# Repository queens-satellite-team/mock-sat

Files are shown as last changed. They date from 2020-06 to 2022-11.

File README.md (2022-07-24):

# Mock CubeSat

The purpose of this repository is to house all software and hardware required to build a Mock-Sat. A Mock-Sat is the Queen's Space Engineering Team - Satellite's hardware and software development platform. A typical use case for this platform is that you have some program or code idea and want to see how it interacts within the spacecraft system, or have some hardware and need to see how it can be integrated within the spacecraft system, you can build a moc-sat and implement your idea on top of the basic design.

## Mock-Sat Functionality

The moc-sat has the following resources are available to users:

- 1-axis orientation control
- image capturing
- one way communication (send beacon signals)

Additional resources to be worked on include:
- system configuration files
- simple two way communication
- command and data handling
- power generation and control
- fault detections
- fault responses
- multi-axis orientation control

## Mock-Sat Repository Layout

### Data Folder
This folder contains all images and text data on board the Moc-Sat. It is broken down into data that is to be sent out via the communications system, and data that is being stored either for testing

### Docs Folder
This folder contains general information and documentation regarding the moc-sat. This includes datasheets and papers that provide some additional theory behind the moc-sat.

### Firmware Folder
This folder contains all software to be put on seperate Arduino and STM32 microcontrollers that implement the different systems available to the moc-sat such as the communications system and the attitude determination and control system.

### Hardware Folder
This folder contains all hardware files, pinout, and wiring diagrams required to build the moc-sat systems.

### Media Folder
This folder contains all images used within this repository.

### SRC (Source) Folder
This folder contains all code written for the moc-sat on the raspberry pi. This includes python implementations for all sub-sytems and the actuall mock-sat itself.

### Tasks Folder
This folder contains all the tasks that the satellite is to perform. See the README instructions in the folder for creating new and how to use them!

# Getting Started
Below are the following steps to setup the software and hardware of the mock-sat.

## Software Setup
### Prerequisites
1. You should have python version 3.7 or greater installed.
2. The raspberry pi should have the latest version of the [Raspberry Pi OS (Buster)](https://www.raspberrypi.com/software/) installed.

You can see what version of python you are using with the following command in a terminal:
```
python3 -V
```

And you can determine which instance of python (as you can have multiple) you are running with the following command in a terminal:
```
which python3
```

### Setting up the Repository
Perform the following steps within a terminal.

1. Clone the repository.
```
git clone https://github.com/queens-satellite-team/mock-sat.git
cd mock-sat/
```

2. Create a python virtual environment. 
```
python3 -m venv moc-sat-venv
```

3. Activate the virtual environment and install all of the required packages.

- a. If you are on MacOS or Raspberry Pi (Linux):
```
source moc-sat-venv/bin/activate
moc-sat-venv/bin/python3 -m pip install --upgrade pip
moc-sat-venv/bin/pip3 install -r requirements.txt
```

- b. If you are developing on Windows:
```
source moc-sat-venv/Scripts/activate
moc-sat-venv/Scripts/python3 -m pip install --upgrade pip
moc-sat-venv/Scripts/pip3 install -r requirements.txt
```

## Hardware Setup
The following hardware is required:
- BLDC Motor, power supply, and motor controller.
- Two transceivers, one for the mock-sat and one for the ground station.
- Raspberry Pi
- Raspberry Pi Camera
- An orientation sensor (MPU650)
- Three Arduinos
- A 1-Axis test bed for the satellite

Please see the README.md in the hardware directory within this repository for further instructions.

## Google Drive 

- https://drive.google.com/drive/folders/1PjCpiJ1GjcGLUgqpvl0FE0fzke4_DoX0?usp=sharing

Meeting notes, logistical documents and other files that may not be in this repository are kept on a
[Google Drive](https://drive.google.com/drive/folders/1PjCpiJ1GjcGLUgqpvl0FE0fzke4_DoX0?usp=sharinghttps://www.google.com). The drive has public view access. If you are a member of QSAT and would like full edit access, please request access on the drive or send an email to joshua.wade@queensu.ca. Or just message me on facebook or something. 

## Repository Style Guidelines
In order to have consistency in the repository we are following the [Google
style guidelines](https://github.com/google/styleguide). The repository is 
primarily [C++](https://google.github.io/styleguide/cppguide.html) and 
[Python](https://google.github.io/styleguide/pyguide.html) but another relevant
style guideline is the [filetypes and names](https://developers.google.com/style/filenames).
If languages other than this are introduced into the repository, please consult
the associated style guideline and adhere to it.

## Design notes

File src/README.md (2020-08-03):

### Source Directory
  - `cmake` CMake configuration files for Arduino-CMake
  - `firmware` Arduino code.
  - `img` Image to send and location to store received image.
  - `scripts` Python scripts.
  - `src` C++ code.

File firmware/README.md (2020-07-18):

# Firmware
This directory contains all source files related to Arduino development. The
build system that is being used is [Arduino CMake](https://github.com/queezythegreat/arduino-cmake).
If you would like to build the code, navigate to the /src directory.
```
mkdir build && cd build
cmake ..
make <name of executable>-upload
```
If you would like to monitor the serial port the executable was uploaded on, 
additionally run:
```
make <name of executable>-serial
```
To use the above command you must have [Picocom](https://linux.die.net/man/8/picocom)
installed. 

## Debugging
The `make <name of executable>-upload` command often fails with the dreaded:
```
avrdude: stk500v2_ReceiveMessage(): timeout
```
This means your system cannot communicate with the serial port that has been
specified, either it doesn't exist (i.e. nothing is plugged in) or another
device is blocking it. Make sure:
* You do not have the Arduino IDE open, this will block the serial port
* There are no other scripts or executables using the serial port
* The Arduino is plugged in
* You have permission to use this serial port on your system
If you are developing on Windows using WSLtty, the serial port can be finicky.
I would suggest following these [instructions](https://docs.microsoft.com/en-us/archive/blogs/wsl/serial-support-on-the-windows-subsystem-for-linux) and then uploading the "Hello World" serial writing example
using the Arduino IDE. Then you can confirm that the serial port is activated
and configured correctly. After that you should be able to build.

## Serial Monitoring
It can be useful to open a serial monitor. Since Arduino CMake requires Picocom,
it makes sense to use that. Modify the following command for your needs:
```
picocom -b 115200 -r -l /dev/ttyUSB0
```
To exit Picocom use <Ctrl-a><Ctrl-x>.
## Adding libraries
The build system will detect external libraries that you use if you install
them in `/usr/share/arduino/libraries`.

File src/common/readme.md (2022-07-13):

# Common 
This folder contains all the common files that can be shared acrosss all sub-system code.

# 1.0 Arduino
The Arduino base class provides serial and i2c communication methods to be shared across any system. 

- More information on serial communication between a raspberry pi and an Arduino can be found [here](https://roboticsbackend.com/raspberry-pi-arduino-serial-communication/)
- More information on i2c communication between a raspberry pi and an Arduino can be found [here]()

## 1.1 Usage
We are leveraging Python's [class inheritance](https://www.w3schools.com/python/python_inheritance.asp) so that all our systems (radio, reaction wheel, etc.) can have the same communication method between the raspberry pi and the Arduino microcontrollers that implement the system. We can create a Python class that represents a system and inherent all methods from the Arduino class as seen below:

```
class Radio(Arduino):
    '''Radio sub-system to control an RF24 radio.
    '''

    def __init__(self):
        super().__init__()  # call the init function of the parent Arduino class
    
    def transmit(self, data:str):
        self.send_over_serial(data) # use the Arduino's class method to send over serial
```

## 1.2 Hardware Connections
Use the following image to setup the hardware connection between the raspberry pi and the Arduino.Be careful during this step! Arduinos use 5V-logic and Raspberry Pis use 3V3-logic. Fortunatly, the Raspberry Pi has internal pull-up resistors on the I2C lines, which pull the bus up to 3.3-volts. As long as you don’t connect any devices that pull the levels up to 5-volts you will be OK. You should also note that Arduino has open-collector outputs. Because of this, the Arduino logic levels on its I2C bus will be set to the levels of the pull-ups, which in this arrangement are in the Raspberry Pi. However, this does not work for serial communication! Please note the logic level converter in the Serial GPIO photo.

### 1.2.1 Serial (USB)

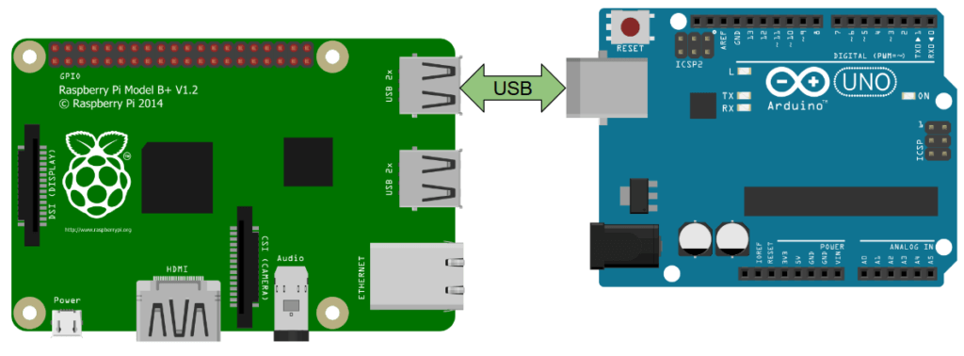
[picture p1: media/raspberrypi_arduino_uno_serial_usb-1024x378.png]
serial_pi_arduino


### 1.2.2 Serial (GPIOs)
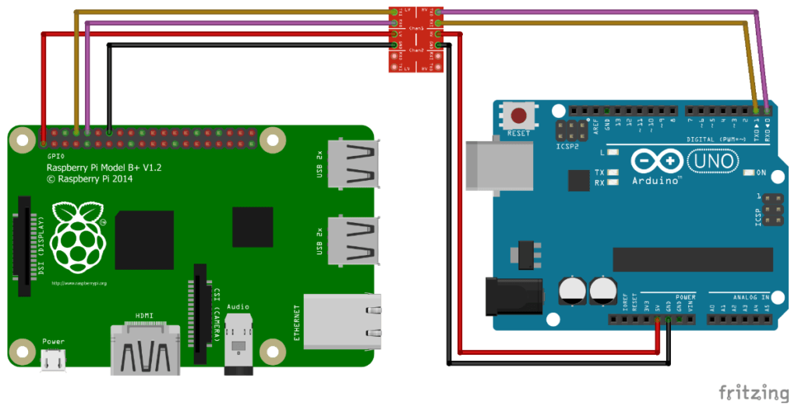
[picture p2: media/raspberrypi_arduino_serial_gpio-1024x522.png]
serial_pi_arduino


### 1.2.3 I2C (GPIOs)
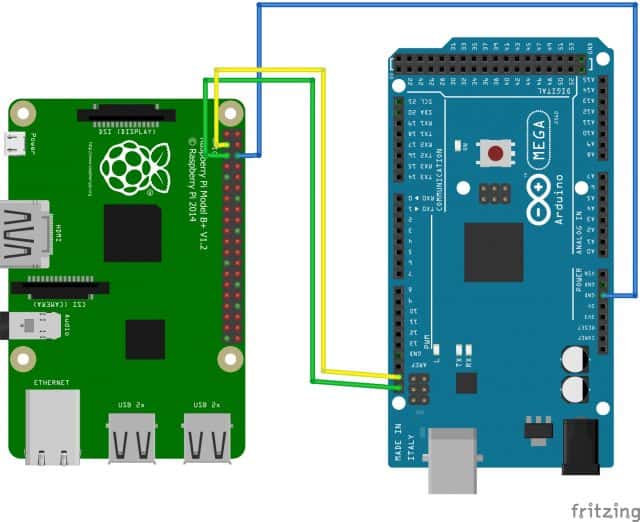
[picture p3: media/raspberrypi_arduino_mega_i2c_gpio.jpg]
serial_pi_arduino


# 2.0 Satellite
This is our mock-sat python object. It reflects all the hardware capabilities of the mock-sat, and provides the functionality to control these hardware features. The mock-sat object is available to all tasks scheduled by the OBC task manager and can thus use all methods and attributes of the class. 

# 3.0 Logger
This is our main way to log and print out all debug, info, warning, and critical messages. This class prints messages to the terminal screen (stdout), and saves it to a log file called by defualt "logger.log".

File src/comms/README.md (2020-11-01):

# Mock Sat - Communications

The purpose of this repository is to keep track of work and issues while building the communication software for a working (non-flight ready) satellite.

## Implementation

Four files are required to operate the MOC-SAT Communications. These include:

1. ground_station.py
2. ground_station.ino

3. satellite.py
4. satellite.ino

### ground_station.py

Opens a GUI that enables the user to send various commands to the connected tranceiver. The GUI has a serial monitor that can read data received from the connected arduino through the serial connection.

Upload this script to a computer (base station) and change hardware settings under CONFIGURATION in file.

### ground_station.ino

The connected Arduino and radio receives command from GUI and implements the respected command. The Arduino first sends an OP_CODE to the satellite's transeiver and then waits to receive data from the satellite.

Upload this script to the arduino (base station) and change hardware settings under Hardware Config and Radio Config in file.

### satellite.py

Reads an OP_CODE from the connected transceiver and executs an instruction according to it.

Upload this script to a rasperryPi (satellite) and change hardware settings under CONFIGURATION in file.

### satellite.ino

The connected Arduino and radio receives command from the base station transeiver and forwards it to the OBC (satellite.py). The Arduino then transmits the data corresponding to the received OP_CODE to the ground station transeiver.

Upload this script to the arduino (satellite) and change hardware settings under Hardware Config and Radio Config in file.

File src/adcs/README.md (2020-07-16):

The following scripts rely on:

-the RPi.GPIO library for python control of raspi IO pins (often comes pre-installed on raspi)
-the adafruit_bno055 library (for reading BNO055 sensor)
-all other libraries should be installed with python3

`BNO055_TEST.py` 
-tests the i2c connection between the raspi and the BNO055 sensor (currently tested with DFRobot's Gravity BNO055 sensor)

`FIT0441_TEST.py`
-tests the PWM control of the FIT0441 motor + controller unit - note that PWM uses pin 18 as that is the only harware PWM pin on the raspi 3B+

`MAX_TRQ.py`
-generates maximum change in reaction wheel momentum - used to test viability of testing platform

`PID_TEST.py`	***DISCONTINUED***
-initial attempt at PROPORTIONAL control of satellite orientation (single axis) - discontinued due to faulty testing bed (1st iteration gimbal)

`P_TEST.py`	***DISCONTINUED***
-second attemp at PROPORTIONAL control of satellite orientation (single axis), attempted patches for faulty testing bed - discontinued due to dampening of testing bed (2nd iteration gimbal)

`PI_TEST.py`
-partially working PROPORTIONAL-INTERGRAL control of satellite orientation (single axis) - tested using string testing bed

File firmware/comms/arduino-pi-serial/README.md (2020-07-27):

# Arduino-Pi comms testing

I'm currently working on reading files from the raspberry pi and sending to an arduino nano via serial port.

Serial comms between the pi and nanos is working, but needs to be made more robust.
The current nRF24 comms is happening with a simple transmit/receive data spam setup.
I've been testing using nRF24 ACK packets which seem to do the trick for bidirectional communication, just have to get it working properly and put all the pieces together.

It's taking a little longer than expected and the code is unorganized right now. I'll try to right a better setup guide and organize everything once it's all working

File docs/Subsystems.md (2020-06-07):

# QSET - Satellite Team Subsystems

A CubeSat can be broken into six major subsystems: structure, communication, power, attitude determination and control, command and data handling, and the payload. In the past, QSAT has had an exec team of managers for each subsystem and a CTO. QSAT&#39;s goal is to create a CubeSat that can rotate itself and take pictures at given orientation. This involves designing and building each of the subsystems and the computer system that would connect them.

[More info on CubeSat Subsystems](https://www.fictiv.com/blog/posts/satellite-101-what-is-a-cubesat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,data%20handling%2C%20and%20the%20payload.)

## ADCS – Attitude determination and Control System

&quot;_The attitude determination and control system (ADCS) controls the orientation of the CubeSat with respect to an inertial frame of reference and includes reaction wheels, magnetorquers, thrusters, star trackers, sun and Earth sensors, angular rate sensors and GPS receivers and antennas. This complex system is needed because when the satellite is first deployed, for example via NanoRacks from the International Space Station, it is tumbling. Some CubeSats can operate in this state, but others require pointing accuracy and location knowledge.&quot;_

During the first CSDC that Queen&#39;s participated in, the CubeSat only required passive attitude stabilization. (For this reason, the ADCS was just a couple long magnets.) The new ADCS requires active attitude actuation and momentum dumping. The current design includes a setup with 10 sun sensors, a BNO055 Absolute Orientation Sensor, 4 reaction wheels (1 redundant) and 3 magnetorquers. The goal is for the ADCS to provide precise attitude control with the reaction wheels and detumbling with the magnetorquers.

## _Comms – Ground to Sat Communications System_

&quot;_The communications system (COM) is severely limited by the amount of power available, which is usually around 2W. Compared to Boeing&#39;s 702SP Spacecraft, which uses a Xenon Electrostatic ion thruster system (XIPS), operates in the low- to mid-power range of satellites, and has three to eight kilowatts of power, CubeSats&#39; power is exponentially less._

_CubeSats use radio-communication systems in VHF, UHF, F-, S-, C- and X-band. The satellite uses an antenna, usually deployed once in orbit to help with communication. Antennas range from commercial measuring tape to more complicated inflatable dish antennas.&quot;_

## _EPS – Electrical Power System_

&quot;The electrical power system (EPS) consists of solar panels and batteries. Solar panels hold solar cells that convert the solar light from the sun to electricity. Batteries take up a lot of mass and volume on the already tightly packed CubeSat. A major design challenge is placing the solar panels, either on the sides of the CubeSat itself, or having deploying solar panels. Having deployable panels adds solar cell area but also an extra mechanical complexity. For the panels to deploy, they need a burn wire release mechanism, and every mechanical system adds the possibility of a failure. If the panel does not deploy properly, the CubeSat will not have any power and even if everything else is functioning properly, the CubeSat will fail due to the lack of power.&quot;

## _OBC – Onboard Computer System_

The OBC is the system that runs the CubeSat&#39;s software and connects and controls all the other subsystems. &quot;An OBC primarily consists of a microprocessor, memory banks and interfacing chip to connect the computer to other sub-systems.&quot;

Last year, most of the work and research on the OBC involved designing a system that was radiation hardened with redundant processors and bit voting logic. This was intended to rectify potential bit switching caused by ionizing radiation in LEO. Unfortunately, the complexity this created is beyond the scope of what QSAT is trying to accomplish this year, so the focus will be on creating a traditional OBC.

[More OBC info](https://blog.satsearch.co/2020-03-11-overview-of-on-board-computers-available-on-the-global-space-marketplace)

## _Payload – Camera and Telescope_

&quot;_The payload, or the purpose of the CubeSat, dramatically varies, depending on the type of mission required. These can include cameras for pictures or video, like Planet Labs, or space qualification of certain electronic components, testing of a flight control system, or even some type of biological experiment.&quot;_

QSAT&#39;s current mission is to create a satellite that can take pictures of the Earth. For this reason, the payload is essentially a camera sensor and a focusing lens. Pictures taken by the camera also need to be stored on the sat until they can be downlinked to the command station.

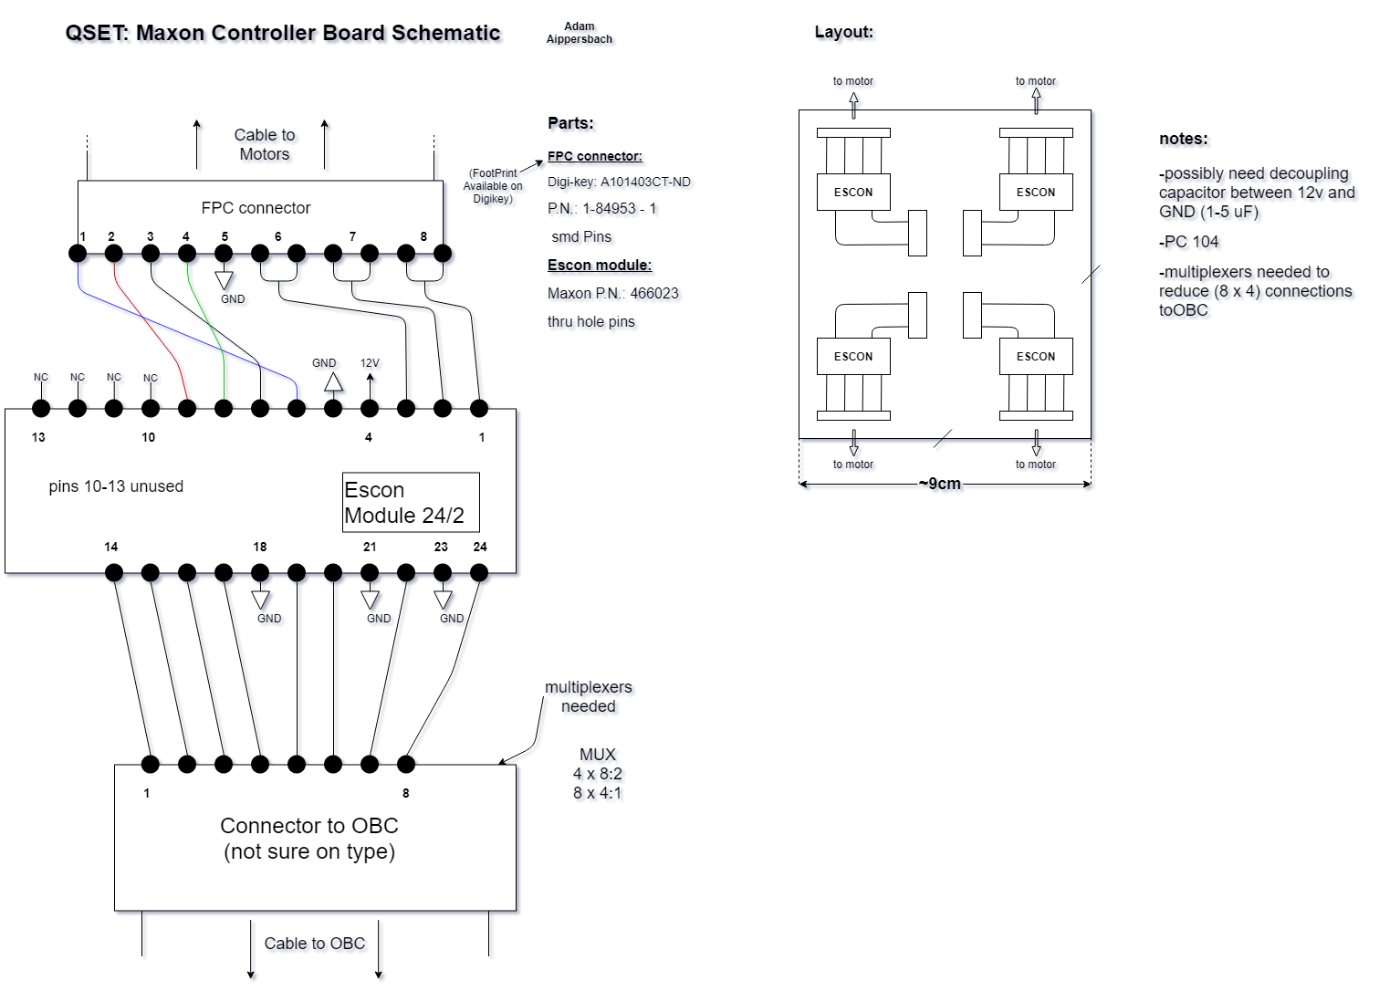
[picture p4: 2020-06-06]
docs/ADCS/Schematics/Maxon Controller Board Schematic.png

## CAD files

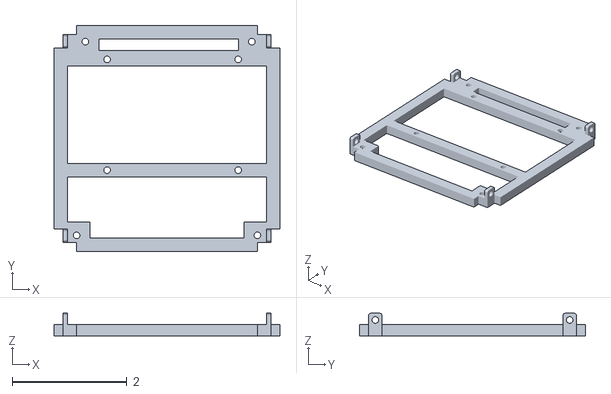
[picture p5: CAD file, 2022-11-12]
hardware/mock-sat-1U/stl/shelf-rpi.stl
3.94 x 3.94 x 0.394

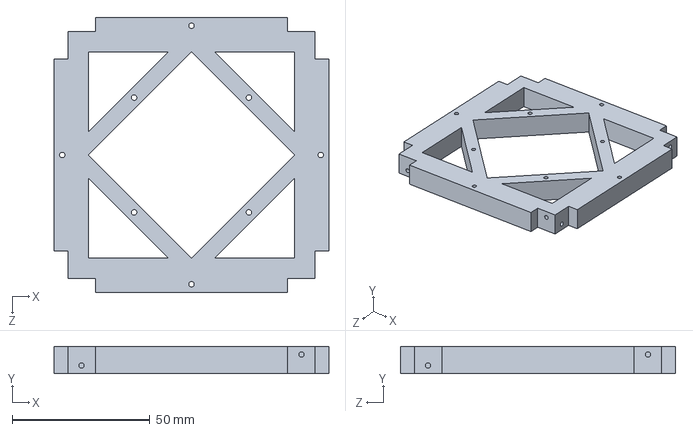
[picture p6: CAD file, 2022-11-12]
hardware/mock-sat-chassis/baseplate 2.SLDPRT
100.0 x 10.0 x 100.0 mm

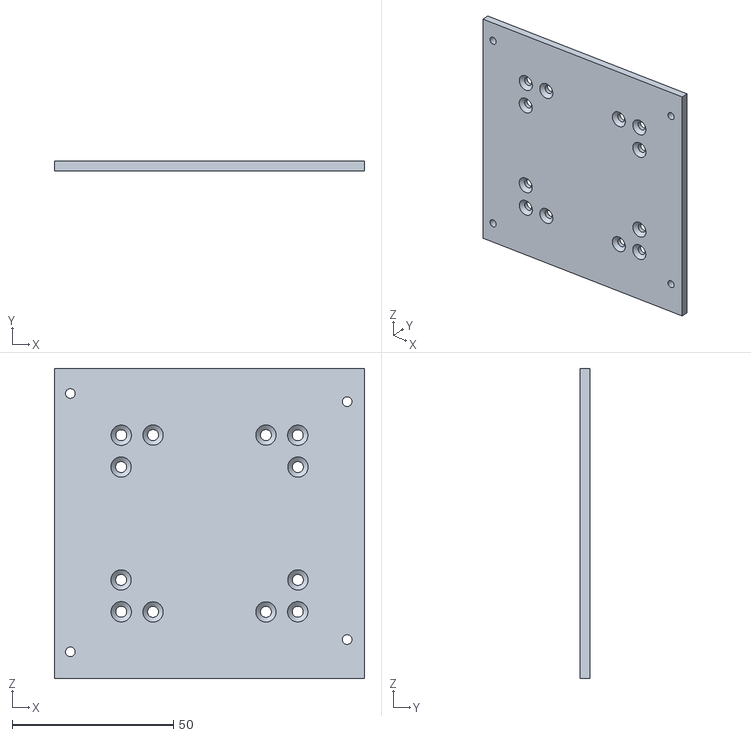
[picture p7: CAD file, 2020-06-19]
hardware/satellite-frame/base-plate-pc104.stl
96.0 x 3.00 x 96.0

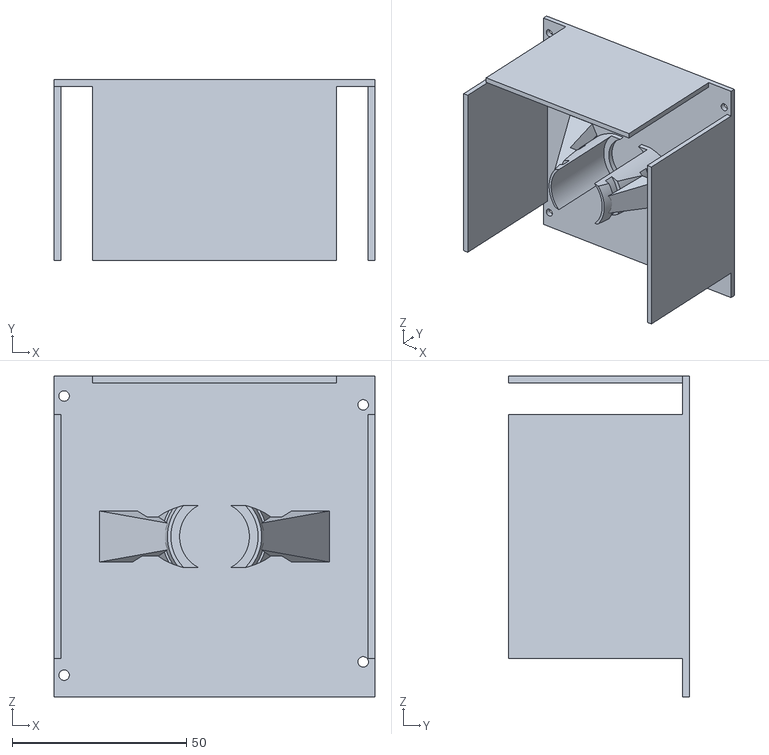
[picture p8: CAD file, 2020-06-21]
hardware/testing-gimbal/prototype/fit0411-motor-frame.stl
92.0 x 52.0 x 92.0

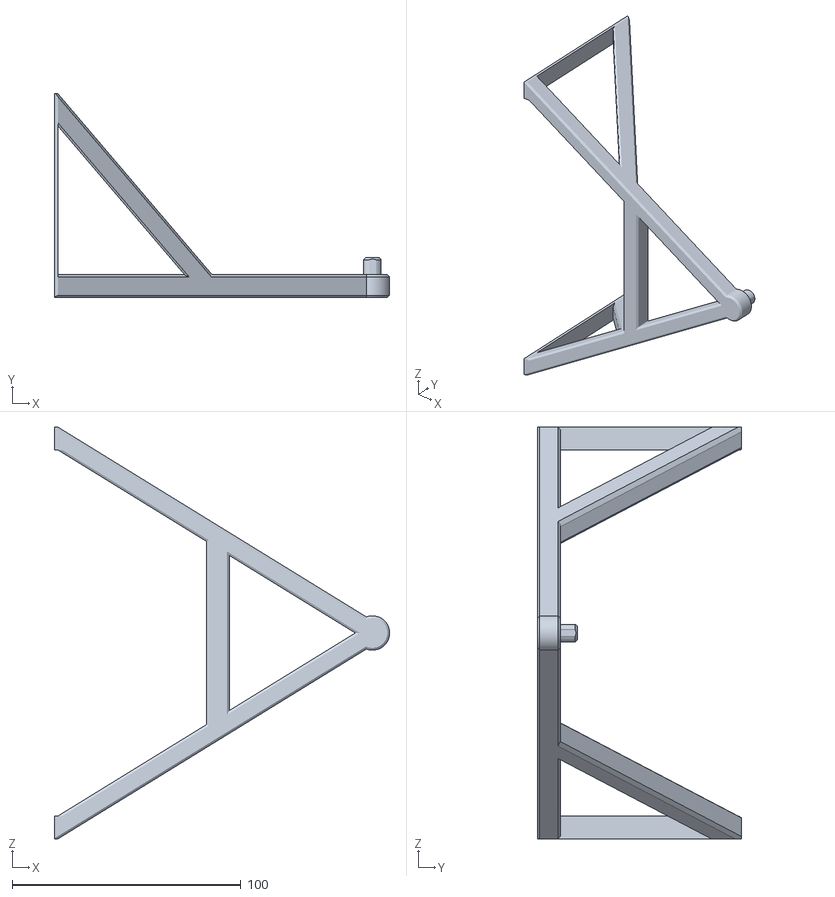
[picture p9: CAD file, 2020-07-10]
hardware/testing-gimbal/secondary-model/GimbalMk2 - gimbal base-1.STL
146.5 x 89.2 x 180.0

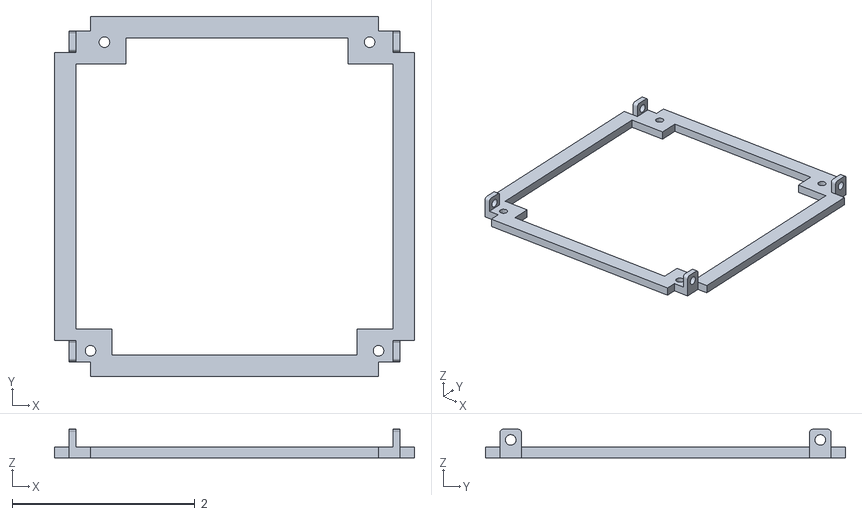
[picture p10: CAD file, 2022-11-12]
hardware/mock-sat-1U/stl/shelf-blank.stl
3.94 x 3.94 x 0.315

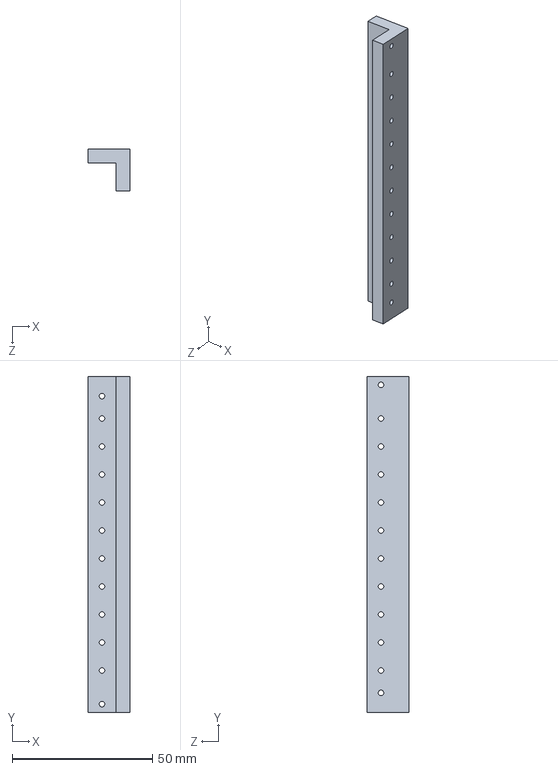
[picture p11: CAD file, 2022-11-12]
hardware/mock-sat-chassis/Siderib-U.SLDPRT
15.0 x 120.0 x 15.0 mm

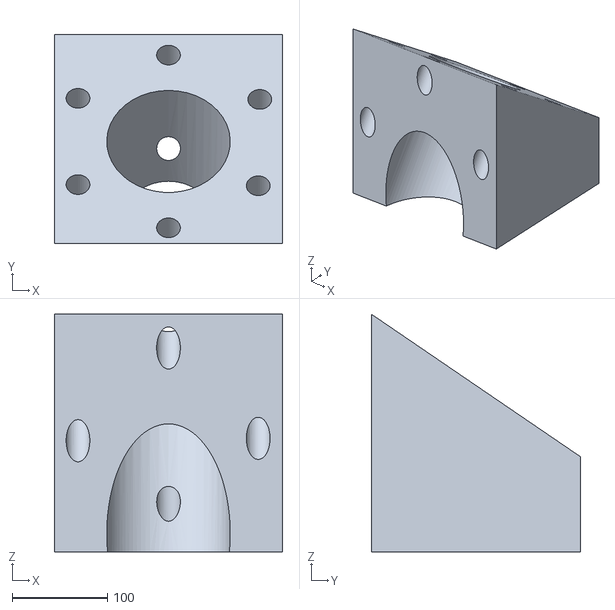
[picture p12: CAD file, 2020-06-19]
hardware/satellite-frame/reaction-wheel-mount.stl
240.0 x 220.0 x 250.0

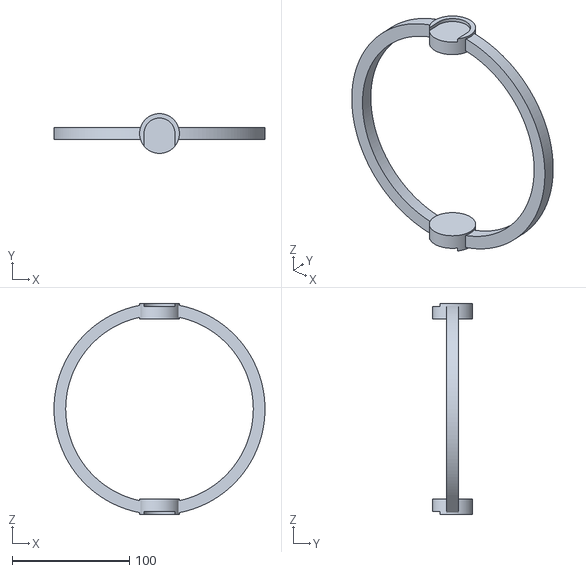
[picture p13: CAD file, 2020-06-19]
hardware/testing-gimbal/prototype/inner-ring-1.stl
180.0 x 34.0 x 180.0

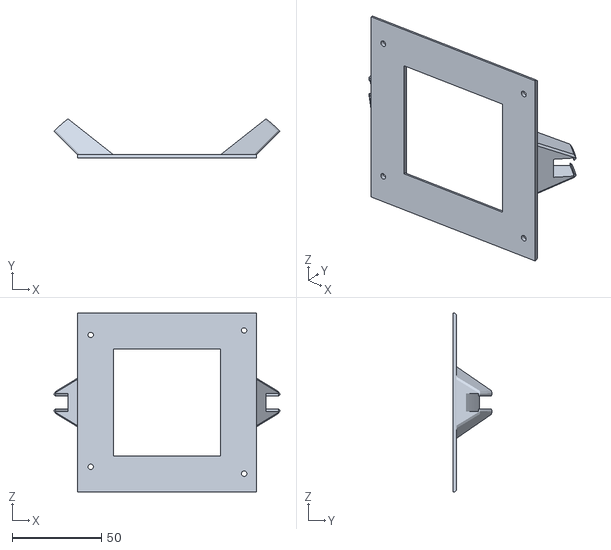
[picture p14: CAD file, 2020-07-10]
hardware/testing-gimbal/secondary-model/GimbalMk2 - connection-1.STL
126.3 x 22.0 x 100.0

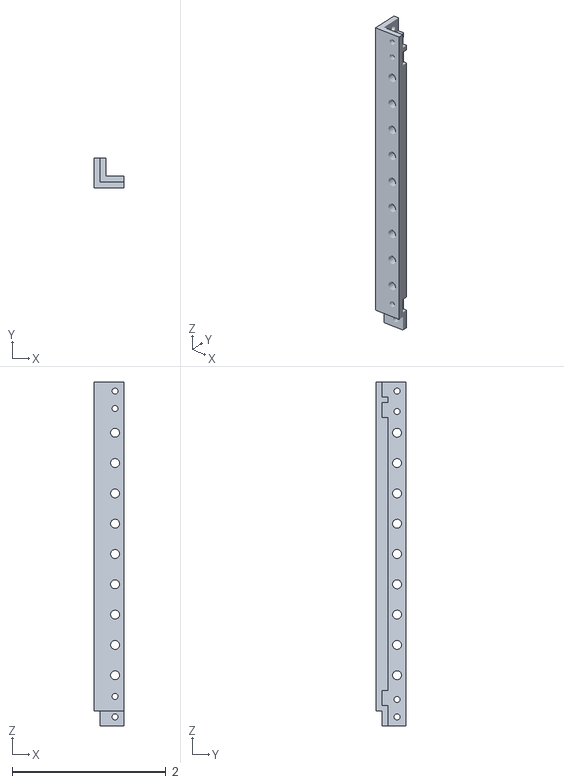
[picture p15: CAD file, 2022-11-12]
hardware/mock-sat-1U/stl/rail.stl
0.394 x 0.394 x 4.47

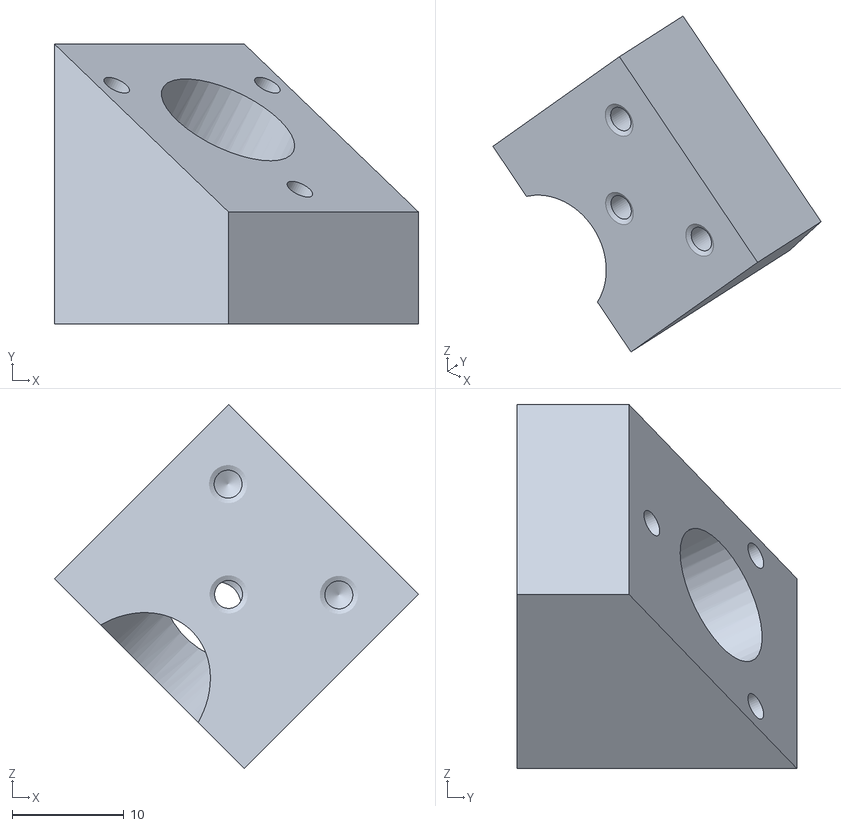
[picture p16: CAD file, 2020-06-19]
hardware/satellite-frame/motor-base.stl
32.5 x 25.0 x 32.5

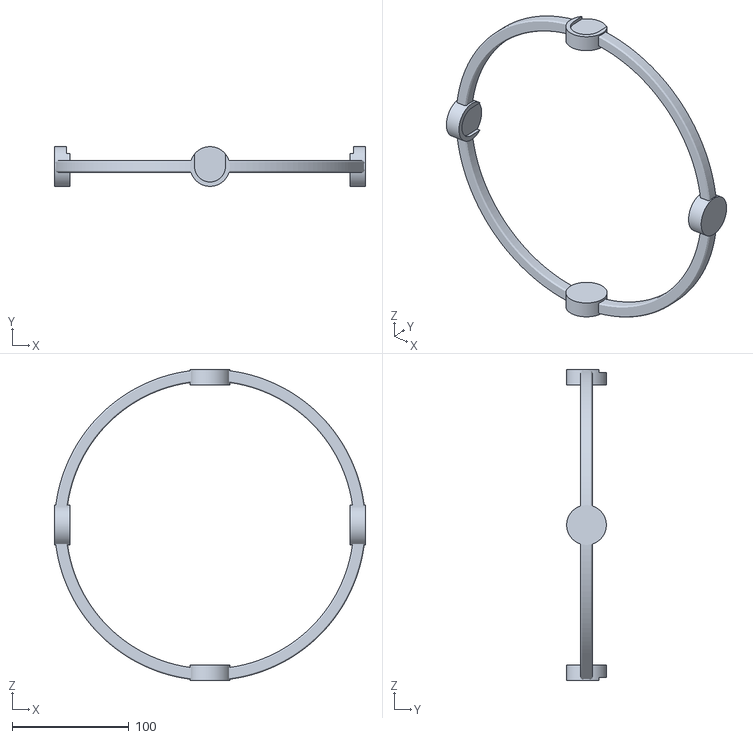
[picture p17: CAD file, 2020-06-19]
hardware/testing-gimbal/prototype/outer-ring-1.stl
266.0 x 34.0 x 266.0

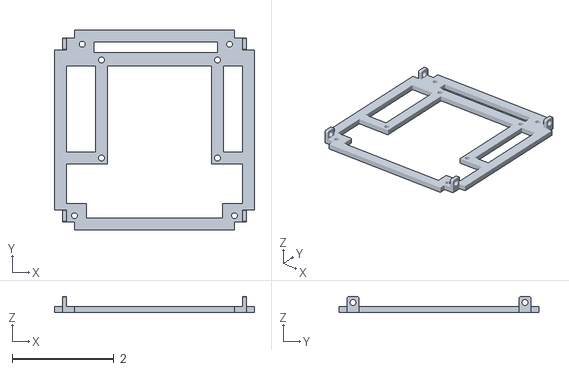
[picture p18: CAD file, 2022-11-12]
hardware/mock-sat-1U/stl/shelf-rpi-2.stl
3.94 x 3.94 x 0.315

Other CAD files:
hardware/testing-gimbal/secondary-model/GimbalMk2 - connection2-1.STL
hardware/satellite-frame/reach-wheel-base-plate.stl
hardware/testing-gimbal/prototype/outer-bearing-clip-1.stl
hardware/testing-gimbal/secondary-model/GimbalMk2 - outer section mk2-1.STL
hardware/mock-sat-1U/stl/rack.stl
hardware/mock-sat-1U/stl/shelf-nucleo.stl
hardware/mock-sat-1U/stl/shelf-protoboard.stl
hardware/mock-sat-chassis/Siderib-U.STL
hardware/testing-gimbal/prototype/inner-bearing-clip-1.stl
hardware/testing-gimbal/prototype/mid-ring-1.stl
hardware/testing-gimbal/secondary-model/GimbalMk2 - KFL08-1 608RS-1.STL
hardware/testing-gimbal/secondary-model/GimbalMk2 - inner section mk2-1.STL
hardware/testing-gimbal/secondary-model/GimbalMk2 - mid section mk2-1.STL

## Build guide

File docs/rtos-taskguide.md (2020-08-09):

List of tasks to run on Arduino FreeRTOS for moc-sat single axis system
-

1. ADCS read and control

    - read BNO055 (through I2C)
    - read Light Sensors
    - read Current Motor Data (read two analog)
    - set enable and direction (set two digital)
    - set desired vel (PWM for arduino or analog through I2C DAC)
    - set desired acc (analog through I2C DAC)

2. Focus and take photo

    - currently a raspi cam, will this work via arduino?
      - if not should we have a master raspi to take photos when the arduino returns okay?
      - would we be able to setup communication with the pi while using FreeRTOS?

3. Transmission of desired direction vector

    - is the transmitter controlled by SPI? 
    - this value should be given to ADCS function (then perhaps increase ADCS function priority?)

4. Transmission of photo information

    - likely the most intensive function/operation
    - can this be set as a 'background process' do be done in chunks? or should it be done all at once?
    
5. Emergency stop

    - simply a high priority function that can read a button or remote signal and stop all processes

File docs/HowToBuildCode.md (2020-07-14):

### Arduino Code
The Arduino code uses the [Arduino CMake](https://github.com/queezythegreat/arduino-cmake)
build system. To make sure the build system is working correctly perform the
following:
#### Linux
* Install CMake and the Arduino SDK. Install `picocom` if you do not already
  have it by running `sudo apt install picocom`. `picocom` is the default
  serial monitor for the build system.
* Connect an Arduino Mega 2560 to your computer. If you are going to connect
  a different Arduino, you must edit the `BOARD` parameter in
  `test/CMakeLists.txt` to reflect the Arduino you are using. If the Arduino
  is using a port other than `/dev/ttyACM0` you must change the `PORT` parameter
  in the same file.
* In the root of the repository, run the following commands:
  ```
  mkdir build && cd build    # create a build directory
  cmake ..                   # run CMake on the parent CMakeLists.txt
  make upload                # upload the firmware to the Arduino
  make hello_world-serial    # run a Picocom terminal to monitor the serial port
  ```
  You should see `Hello World!` being printed every second. To exit the picocom
  terminal, press Ctrl-a Ctrl-x.
#### WSLtty
WSLtty does offer support for communicating with hardware through serial ports.
WSL automatically maps the `COM<N>` ports on Windows to `/dev/ttyS<N>` ports. 
For example, `COM7` would be mapped to `/dev/ttyS7`. You can check which `COM`
port is being used by going into `Device Manager` and checking the 
`Ports (COM & LPT)` header in Windows. If the port being used is `COM7`, then
you must run:
```
sudo chmod 666 /dev/ttyS7
```
then follow the instructions for Linux. Check [this](https://docs.microsoft.com/en-us/archive/blogs/wsl/serial-support-on-the-windows-subsystem-for-linux) for more information.

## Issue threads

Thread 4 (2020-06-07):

Get hardware and tools from QSET room

JoshW7, 2020-06-07:
Email Simon to request temporary access to QSET room. We probably wont be able to get access again, so I need a full list of everything we need for the summer. I can include this list in the email to Simon.

**For Moc-Sat:**
- BLDC Motor, power supply, and motor controller
- Raspberry Pi
- Raspberry Pi Camera
- An orientation sensor
- An Arduino (I also have one of these at home if I can't find any in the room for some reason)

**Also Need:**
- Pelican case with Satellite and other expensive components
- Wires
- Wire cutters
- breadboards
- simple electrical components like resistors, caps
- Maybe soldering equipment

JoshW7, 2020-06-19:
Got most of what was listed, except for Raspberry Pi and capacitors. Pictures of every borrowed item on the [Google Drive](https://drive.google.com/drive/folders/1FAAZQhhic6-W0kydOLPNARDHKofG3PDZ?usp=sharing).

Closed 2020-06-19.

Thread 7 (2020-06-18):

Send low resolution image between transceivers

anthonysteel, 2020-06-18:
Send a low resolution image downloaded from the internet between the transceivers.

anthonysteel, 2020-06-18:
I am going to try a black and white image first.

anthonysteel, 2020-06-18:
It looks like I need to save the image on an SD card, load the image from the SD card onto the Nano and then send the image in packets through the transceiver. I bought [these](https://www.amazon.ca/Gikfun-Storage-Memory-Arduino-EK1442C/dp/B071D5BFKD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).

anthonysteel, 2020-06-21:
I am now using a Mega connected to the SD card and a Nano connected to the nRF24L01 transceiver.  The reason for having two Arduino's is that both the SD card and transceiver communicate using SPI and there is only one SPI port on the Mega/Nano. I am going to try and connect the two boards via I2C.

anthonysteel, 2020-06-25:
I am going to close this issue. To resolve this issue there are actually several sub-issues which are better organized in a project.

Closed 2020-06-25.

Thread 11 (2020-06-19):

Write P Controller to Rotate Satellite in Gimbal

anthonysteel, 2020-06-19:
Convert controller previously used in simulation to controller on satellite.

WoJiaoCal99, 2020-07-16:
Semi-functional PI control working with FIT0441 motor and low-torque (string) testing bed 73f6b52cfca69930f2f6613d548babe2d8815373 .

Closed 2020-07-16.

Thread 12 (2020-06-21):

Find way to work with Soldiworks part files collaboratively

anthonysteel, 2020-06-21:
Part and assembly files are usually large. If you put them in a Github repository it will make pulling and pushing extremely slow especially because git diff won't work on part files. We should decide on a work around for this.

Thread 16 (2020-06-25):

Send Image from SD Card to transceiver on MocSat

anthonysteel, 2020-06-25:
The MocSat has two arduinos, a Mega and a Nano. The Nano is connected to the transceiver and the Mega is connected to an SD card storing the image. The two MocSat Arduinos communicate through an I2C connection. Send the image from the SD card on the Mega to the Nano.

anthonysteel, 2020-07-15:
I stopped using the SD card because it introduced another Arduino unnecessarily. The SD card connection was happening over SPI and there is only one SPI port on the Arduino, which is currently being used by the transceiver. Right now the image is sent over serial to the Arduino. In future an SD card can be incorporated.

Closed 2020-07-14.

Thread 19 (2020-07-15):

Change send/receive scripts to accept ports as inputs

anthonysteel, 2020-07-15:
Right now the ports that the Arduinos are connected on are hard coded in the CMakeLists and in `send.py` / `receive.py`. Change these to accept the port as an input for easier development across machines.

anthonysteel, 2020-07-15:
For example, in the CMakeLists.txt file there is the following:
```
generate_arduino_firmware(server
    SKETCH server.cpp
    PORT /dev/ttyS9
    SERIAL picocom @SERIAL_PORT@
    BOARD mega2560)

generate_arduino_firmware(client
    SKETCH client.cpp
    PORT /dev/ttyS9
    SERIAL picocom @SERIAL_PORT@
    BOARD mega2560
```
which generates two executables, client and server. It would be better if port was specified at build time. Something like:
```
cmake --send-port /dev/ttyS8 --receive-port /dev/ttyS9 ..
```
CMake should have support for this kind of thing, or it can be set as an environment variable which CMake captures.

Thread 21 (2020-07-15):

Add message protocol to transceivers

anthonysteel, 2020-07-15:
As mentioned in #17, some of the image is being lost in transmission. This means it is time to implement some sort of data link layer. [Radiohead](https://www.airspayce.com/mikem/arduino/RadioHead/) seems promising and has support for our nRF24L01. I am going to start by trying to get this [client](https://www.airspayce.com/mikem/arduino/RadioHead/nrf24_client_8pde-example.html) and [server](https://www.airspayce.com/mikem/arduino/RadioHead/nrf24_server_8pde-example.html) example working.

anthonysteel, 2020-07-15:
Got example uploaded to Arduinos in 443d3faa84f1599c5d784021dcd5d4ff76f27415. Example is not working, the transceivers don't seem to able to find each other right now.

anthonysteel, 2020-07-15:
Problem solved, tutorial working, see 2d72ee69961a20e90f34b8c51f3ce3120cf100dc.

anthonysteel, 2020-07-15:
I know have a better understanding of how the transceiver code should work. The Arduino's should blindly read information from the serial port when it is available and blindly read information from the transceivers when it is available. This means that the code for both transceivers can be the same. I pushed this change in 3734c5e0c75544b7baac2652d4e5c5ac71579424.

anthonysteel, 2020-07-16:
Check out how to get [KISS](https://pypi.org/project/kiss/) for python working later. I tried the example but the library seems to be failing right now. The scripts throws a:
```
AttributeError: 'Frame' object has no attribute 'text'
```
from the APRS python package.

Closed 2020-07-18.

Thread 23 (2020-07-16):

Create new STL files for mounting maxon motor and drivers to sat frame

WoJiaoCal99, 2020-07-16:
Design a mount for prototyping with a single maxon motor and driver instead of FIT0441 motor

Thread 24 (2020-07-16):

Get single axis PI control loop working with maxon motor

WoJiaoCal99, 2020-07-16:

WoJiaoCal99, 2020-07-19:
Good [article ](https://www.maxongroup.co.uk/maxon/view/news/How-to-configure-a-maxon-ESCON-Speed-Controller) for basics of configuring maxon controller

WoJiaoCal99, 2020-07-19:
Motor [Datasheet ](http://edge.rit.edu/edge/P13021/public/DDR/Maxon%20Generator%2030W.pdf)

WoJiaoCal99, 2020-07-19:
[Page](https://www.maxongroup.com/maxon/view/content/escon-detailsite) for download of maxon controller setup software

anthonysteel, 2020-07-20:
Looks good.

WoJiaoCal99, 2020-07-23:
The [controller](https://www.maxongroup.com/maxon/view/product/control/4-Q-Servokontroller/466023) requires multiple inputs as specific signals:
-desired angular velocity (analog or digital PWM)
-angular acceleration (analog)
-direction (digital)
-enable (digital)
-all outputs come as analog
The raspi can only create digital and PWM signals (PWM with limited accuracy), thus cannot set angular acceleration. Simplest solution is probably an i2c slave to read and write analog signals and relay back to raspi.

WoJiaoCal99, 2020-07-23:
The motor connects via flex-cable (FPC cable) and needs an adapter for prototyping. [This 11-pin adapter](https://www.digikey.ca/en/products/detail/1-1734248-1/A101417CT-ND/2567553?itemSeq=333183093) should have the right spacing for the 5 normal width connections, and 3 wide (motor winding) connections on the flex cable.

WoJiaoCal99, 2020-08-06:
A few developments for maxon motor control:
-Previous adapter is a surface mount connector for PCBs. [This version](https://www.digikey.ca/en/products/detail/te-connectivity-amp-connectors/1-84982-1/1893492) should have enough space for soldering and prototyping.
-[This DAC](https://www.digikey.ca/en/products/detail/maxim-integrated/MAX11300PMB1%23/4914312?productid=4914312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) currently only works with the [Munich GUI Software](https://www.maximintegrated.com/en/design/software-description.html/swpart=SFW0004100C) on a laptop. [This library](https://os.mbed.com/teams/MaximIntegrated/code/MAX113XX_Pixi/shortlog/) seemed promising but hasn't worked with the raspi thus far. It should be noted that the DAC can be used as an oscilloscope and analog/digital signal IO and would be useful to have working with either raspi/arduino for both prototyping and potentially sensor/motor control in the final version of the moc-sat.
-Moving forwards with the [Sparkfun MCP4725 DAC](https://www.sparkfun.com/products/12918). If we can create our own i2c communication protocol with the chip, we could print our own on a custom PCB based on the [public design](https://github.com/sparkfun/MCP4725_Breakout/tree/v14).
-Moving from raspi to arduino for compatibility with the new DAC, as well as future development including RTOS and integration with the OBC subteam.

WoJiaoCal99, 2020-08-14:
Motor is now working:
-acc and vel are controlled by two MCP4725 DACs
-second flex-cable connection can be soldered for motor connections
-All i2c connections have been tested with arduino's [freeRTOS](https://www.freertos.org/a00110.html) and work - see commit 09b34a6a7239b34cd3f976704b3c3b82ddb7321e
-Moving forwards by creating control loop function to be run by the RTOS

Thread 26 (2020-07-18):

Create a packet format and checksum for transceivers

anthonysteel, 2020-07-18:
I was able to get an image sent between the two Arduinos using a physical I2C connection. The program for this was very simple. Parse the stream of bytes coming from the image file into buffers that do not exceed the serial buffer on the Arduino. Then have code on the Arduinos to receive bytes over I2C and send them onto the serial port.

However, when I tried to use the same program over the transceivers, a bunch of bytes were dropped. There could be more than one reason for this, but I think that implementing some kind of message protocol between the Arduino's would be the easiest solution.

The current code for the Arduino's is [here](https://github.com/queens-satellite-team/moc_sat/blob/master/src/firmware/transceiver.cpp) and looks like this:
```C++
#include <Arduino.h>
#include <SPI.h>
#include <RadioHead.h>
#include <RadioHead/RHGenericSPI.h>
#include <RadioHead/RH_NRF24.h>

RH_NRF24 nrf24(8, 53);
uint8_t data[RH_NRF24_MAX_MESSAGE_LEN];
uint8_t read_byte = 1;

void setup() {
  Serial.begin(9600);
  while (!Serial);
  if (!nrf24.init()) Serial.println("init failed");
  if (!nrf24.setChannel(1)) Serial.println("setChannel failed");
  if (!nrf24.setRF(RH_NRF24::DataRate2Mbps, RH_NRF24::TransmitPower0dBm))
    Serial.println("setRF failed!");
}

void loop() {
  int i = 0;
  while (Serial.available()) {
    if (i < RH_NRF24_MAX_MESSAGE_LEN) {
      data[i] = Serial.read();
      i++;
    } else {
      nrf24.send(data, sizeof(uint8_t)*i);
      nrf24.waitPacketSent();
      i = 0;
    }
  }
  if (i != 0) {
    nrf24.send(data, sizeof(data));
    nrf24.waitPacketSent();
  }
  while (nrf24.available()) {
    nrf24.recv(data, &read_byte);
    Serial.print(char(data[0]));
  }
}
```
Basically, if bytes are in the serial buffer, send them on the transceiver. If there are bytes in the transceiver buffer send them on serial. The same code can be run on both Arduino's and flashed once. I think this has a lot of upsides for development, and if we can get the image sending using the same Arduino code on the transceivers, that would be really great.

The scripts that parse the files into buffers and sends them over serial is [here](https://github.com/queens-satellite-team/moc_sat/tree/master/src/scripts/comms). The scripts are conveniently called `send.py` and `receive.py`.

In order to handle the seemingly lossy Bluetooth connection, I think we have to define a packet structure. We should implement the [KISS](https://en.wikipedia.org/wiki/KISS_(TNC)) protocol. Basically, choose a character to be a frame begin and end character `0xC0` . Choose a simply algorithm to make a check sum, for example, split each byte into a nibble, XOR all the bytes in the data buffer. Send the message as:
```
 0xC0 - checksum byte - some predefined number of data bytes - 0xC0.
```
Then have a byte that is dedicated as an acknowledge command. One of the scripts sends the message, the other checks the check sum and sends an ack command, if the ack is not sent in a predefined timeout, the message is resent. This should be relatively simple to implement.  The special command bytes, like frame header and acknowledge, will have to be escaped inside the data bytes. The protocol talks about this. Without this if 0xC0 was to appear in the data, there is no way to know if that was meant to be a frame end or actually 0xC0.

@JoshW7, can you tackle this problem?

anthonysteel, 2020-07-22:
See https://github.com/queens-satellite-team/moc_sat/issues/28#issuecomment-662189579

Closed 2020-07-22.

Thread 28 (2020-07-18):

Send image from Raspberry Pi SD card with NRF24L01 Transceiver

JoshW7, 2020-07-18:
I got an Arduino nano with a NRF24L01 set up to work from the Raspberry pi. The nano couldn't communicate with the R Pi using the default linux IDE so I installed the ARM version of Arduino 1.8.0 following this [forum thread](https://www.raspberrypi.org/forums/viewtopic.php?t=170210).

I installed the same nRF24 library on the pi and successfully sent serial data to my laptop using the transceivers.

Once we get [lossless data transmission](https://github.com/queens-satellite-team/moc_sat/issues/26) working, it should be easy to set up on the pi.

anthonysteel, 2020-07-20:
Another option for people working on this if they have a problem with flashing their Arduino using the Raspberry Pi: you can flash the Arduino using any computer or IDE that supports it and then just connect it to the RP, using the RP only for non-firmware development. Assuming that the Arduino code is relatively stable and won't need to be updated frequently,  this is a reasonable option.

I agree once, we get the lossless data transmission working it should carry over with no problems.

JoshW7, 2020-07-22:
RF24 has a built in acknowledgement (ACK) feature that allows for data packets to be sent without data loss. If you have the Arduino RF24 library installed, you can look at some of the ACK example sketches.

This is essentially a built in system for bi-directional communications and I believe it's what we're looking for. I'm going to mess around with sending huge data streams this way and see how fast/lossless it is. If all goes well, I'll try it with an image.

anthonysteel, 2020-07-22:
Perfect.

anthonysteel, 2020-07-22:
I’m going to close out #26 and we can re-open it if the built in R24 functionality fails.

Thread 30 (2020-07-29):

Order parts for EPS

anthonysteel, 2020-07-29:
Decide on what tutorial we are going to follow, and what parts are required. Write a BOM and push it to MocSat docs.

anthonysteel, 2020-07-29:
@varnikaagupta Was [this](https://www.digikey.ca/en/maker/projects/charge-batteries-with-an-arduino/b9d6ff74ecea437da8126d097d680d56) the tutorial Josh was talking about? You will also want to order a soldering iron, solder, rosin flux, solder remover and/or solder wick.

varnikaagupta, 2020-07-30:
Yep, I'll go through and get down all the equipment needed

varnikaagupta, 2020-07-30:
> Decide on what tutorial we are going to follow, and what parts are required. Write a BOM and push it to MocSat docs.

@anthonysteel Since we want to incorporate solar charging for the moc sat, would it be better to start directly with a tutorial like this? https://create.arduino.cc/projecthub/igorF2/solar-charged-battery-powered-arduino-uno-645d89
What voltage solar cells do we currently have?

anthonysteel, 2020-08-11:
Sorry for the late response to this. I don't know which solar cells are in the room, @JoshW7 might know, but I wouldn't worry about using the proper panels. That tutorial looks good, and yes I would say it is preferable to use panels directly.

You will also want to look at what methods there are for a controlled discharge of the batteries when you are testing the circuit. It might be something as simple as connecting them to a motor or light.

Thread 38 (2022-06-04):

Support Arduino Interface Class

SeanTedesco, 2022-06-04:
# Motivation
The Mock-Sat sub-systems are controlled by Arduino microcontrollers. We should have an easy python interface that supports basic communication with Arduinos for all the supported communication protocols.

# TO DO 📖
- [x] Create common directory
- [x] create Arduino base class
- [x] create serial tx and rx functions
- [x] create i2c tx and rx functions
- [x] implement class in comms RF24 parent class
- [x] include readme that demonstrates how-to-use and required setup.

SeanTedesco, 2022-07-13:
The class has been made and implemented. While the instructions can be added to they're good enough to get started.

Closed 2022-07-13.

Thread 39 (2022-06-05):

Mock-Sat Instructions

SeanTedesco, 2022-06-05:
# Motivation ⛰️
If the Mock-Sat is to be used as a development tool, team members must know how to use the tool. This issue will track the necessary work to create instructional content for the Mock-Sats.

# Implementation Ideas 💡
 - I am under the impression that the best way to learn to use a tool is to use it.
 - Stay away from making it a lab, and more of a technology demonstration. This is not meant to be a second Space School.
 - Every folder should have a README page.
- If we are to make more than one of these, we should have a mock-sat "bring up" page (how to build one).

# Steps Forward 🚶‍♂️
- [ ] Create a list of the required functionality for the Mock-Sat.
- [ ] Create initial demonstration / explanation for each functionality.
- [ ] Have a member give feedback and try to use the mock-sat with the previous demonstration/explanation.
- [ ] Iterate demonstration / explanation.
- [ ] Create videos for demonstration / explanation purposes.

# Completion Criteria 💯
- _Have a second/third year make a mock-sat and begin experimenting_

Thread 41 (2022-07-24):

Template Issue

SeanTedesco, 2022-07-24:
### Template Issue To-Do List
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

# Motivation ⛰️
> Provide a short description of the issue and explain why it is required to work on this issue.

# Next Steps 🚶
> Provide a list of steps for someone to complete in order to finish the issue.

- [ ] this is step one
- [ ] this is step two
- [ ] this is step three

# Supporting Material and Resources 📖
> If any links, resources, or past work would be useful include the links here

- [Markdown Style Guide for Creating Issues](https://www.markdownguide.org/basic-syntax/)

# Definition of Done 💯
> Be specific. There should be a concrete change that occurs after this issue is closed. Something is simplified, created, modified, replaced, enhanced, etc.

### Tags
> tag people that should know about this issue

cc: @SeanTedesco @emmapaczkowski

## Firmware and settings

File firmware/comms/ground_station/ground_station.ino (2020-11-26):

/***********************************************************************************/
/******************************** INCLUDES AND GLOBALS *****************************/
#include <SPI.h>
#include <RF24.h>

byte addresses[][6] = {"1Node", "2Node"};

/* globals for loop() */
bool newCommand = false;
String command;

/* globals for recvFromGS() */
bool newData = false;
const byte numChars = 32;
char receivedChars[numChars];

/* global data structure - maximum of 32 bytes can be sent as a packet */
struct dataStruct
{
  /* TYPE        NAME                  USE           BYTE LOCATION    */
  char flag;             //(command / data)           [0]
  char op_code;          //(command number)           [1]
  uint8_t data_len;      //(length of data)           [2]
  uint8_t data_start;    //(character to start)       [3]
  char data[20];         //(actual data)           [4:23]
  unsigned long _micros; //(return trip time)     [24:27]
  uint8_t data_end;      //(character to end)        [28]
} dataPack;

/***********************************************************************************/
/********************************** USER CONFIG ***********************************/
// Radio configuration
// 0 or 1 to distinguish between GRS = 0 and SAT = 1
bool radioNumber = 0;  // sets writing and reading pipe addresses
bool role = 1;         // 1 = transmit, 0 = receive
uint8_t channel = 100; // frequency channel

// Hardware configuration
RF24 radio(8, 10); //CE, CSN
/***********************************************************************************/
/*************************************** setup() ***********************************/
void setup()
{
  configSerial();
  configDataPack();

  radio.begin();
  radio.setPALevel(RF24_PA_HIGH);
  radio.setAutoAck(true);
  radio.setDataRate(RF24_250KBPS); // RF24_1MBPS or RF24_250KBPS

  if (radioNumber)
  {
    radio.openWritingPipe(addresses[1]);
    radio.openReadingPipe(1, addresses[0]);
  }
  else
  {
    radio.openWritingPipe(addresses[0]);
    radio.openReadingPipe(1, addresses[1]);
  }
  radio.stopListening();
}
/***********************************************************************************/
/************************************* loop () *************************************/
void loop()
{
  if (Serial.available())
  {
    // receive the command from the ground station, updates the newData flag
    recvFromGS();

    // if we're done collecting the new data...
    if (newData)
    {

      radio.stopListening();

      if (!radio.write(&receivedChars, sizeof(receivedChars)))
      {
        Serial.println(F("<failed>"));
      }
      else
      {
        Serial.println(F("<success>"));
        newData = false;
      }
    }
  }
  delay(500);
}
/******************************* configRadio ************************************/
void configRadio()
{
  radio.begin();
  radio.setPALevel(RF24_PA_HIGH);
  radio.setAutoAck(true);
  radio.setDataRate(RF24_250KBPS); // RF24_1MBPS or RF24_250KBPS

  if (radioNumber)
  {
    radio.openWritingPipe(addresses[1]);
    radio.openReadingPipe(1, addresses[0]);
  }
  else
  {
    radio.openWritingPipe(addresses[0]);
    radio.openReadingPipe(1, addresses[1]);
  }
  radio.stopListening();
}
/***********************************************************************************/
/********************************* configSerial *********************************/
void configSerial()
{
  Serial.begin(9600);
  Serial.flush();
  Serial.println("<Arduino is ready>");
}
/***********************************************************************************/
/********************************** configDataPack ******************************/
void configDataPack()
{
  dataPack.flag = '0';
  dataPack.op_code = '0';
  dataPack.data_len = 0;
  dataPack.data_start = B10101010;
  dataPack.data_end = B01010101;
}
/***********************************************************************************/
/************************************* recvFromGS() ********************************/
void recvFromGS()
{
  static boolean recvInProgress = false;
  static byte ndx = 0;
  char startMarker = '<';
  char endMarker = '>';
  char rc;

  while (Serial.available() > 0 && newData == false)
  {
    rc = Serial.read();

    if (recvInProgress == true)
    {
      if (rc != endMarker)
      {
        receivedChars[ndx] = rc;
        ndx++;
        if (ndx >= numChars)
        {
          ndx = numChars - 1;
        }
      }
      else
      {
        receivedChars[ndx] = '\0'; // terminate the string
        recvInProgress = false;
        ndx = 0;
        newData = true;
      }
    }
    else if (rc == startMarker)
    {
      recvInProgress = true;
    }
  }
}
/***********************************************************************************/
/********************************** commandOne *************************************/
void commandOne()
{
  Serial.println("Command One Reached"); //debugging

  //debugging
  Serial.print("Updated Data: ");
  Serial.println(dataPack.data);
  Serial.print(" Flag: ");
  Serial.println(dataPack.flag);

  radio.stopListening();

  if (!radio.write(&dataPack, sizeof(dataPack)))
  {
    Serial.println(F("Failed to send Command One"));
  }
  else
  {
    Serial.println(F("Sent Command One"));
    newCommand = false;
  }
}
/***********************************************************************************/
/********************************** commandTwo *************************************/
void commandTwo()
{
  Serial.println("Command Two Reached"); //debugging

  // update the data to be sent
  dataPack.flag = 2;
  dataPack.data[0] = '2';

  //debugging
  Serial.print("Updated Data: ");
  Serial.print(" Flag: ");
  Serial.print(dataPack.flag);
  Serial.print(" Data: ");
  Serial.println(dataPack.data[0]);

  radio.stopListening();

  if (!radio.write(&dataPack, sizeof(dataPack)))
  {
    Serial.println(F("Failed to send Command Two"));
  }
  else
  {
    Serial.println(F("Sent Command Two"));
    newCommand = false;
  }
}
/***********************************************************************************/
/********************************** commandThree ***********************************/
void commandThree()
{
  Serial.println("Command Three Reached"); //debugging

  // update the data to be sent
  dataPack.flag = 3;
  dataPack.data[0] = '3';
  Serial.print("Updated Data: ");
  Serial.print(" Flag: ");
  Serial.print(dataPack.flag);
  Serial.print(" Data: ");
  Serial.println(dataPack.data[0]);

  radio.stopListening();

  if (!radio.write(&dataPack, sizeof(dataPack)))
  {
    Serial.println(F("Failed to send Command Three"));
  }
  else
  {
    Serial.println(F("Sent Command Three"));
    newCommand = false;
  }
} //end_commandThree
  /***********************************************************************************/

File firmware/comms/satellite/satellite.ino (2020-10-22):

/*********************** HARDWARE CONFIG ******************************/
#define CE_pin  7
#define CSN_pin 8
/***********************************************************************/

#include <SPI.h> 
#include <nRF24L01.h>
#include <RF24.h> 

byte addresses[][6] = {"TxAAA","RxAAA"};
bool newData = false;
bool newCommand = false; 
String command; 
const byte numChars = 32;
char receivedChars[numChars];
uint8_t chann = 81; 
bool role = 0; 

struct dataStruct{
  char _tag;
  float _value; 
} dataPack;

/*********************** RADIO CONFIG ***********************************/
// Radio configuration
// 0 or 1 to distinguish between Tx = 0 and Rx = 1
bool radioNumber = 1; 

// Hardware configuration:
RF24 radio(CE_pin, CSN_pin);
/***********************************************************************/

void setup() {
  // ESTABLISH RADIO PARAMETERS
  radio.begin();
  radio.setPALevel(RF24_PA_HIGH);
  radio.setAutoAck(true);
  radio.setChannel(chann); //0-125
  radio.setDataRate( RF24_250KBPS );
  radio.setRetries(3,5); //delay, count
  if(radioNumber){
    radio.openWritingPipe(addresses[1]);
    radio.openReadingPipe(1,addresses[0]);
  }else{
    radio.openWritingPipe(addresses[0]);
    radio.openReadingPipe(1,addresses[1]);
  }
  radio.startListening();

  //SETUP SERIAL CONNECTION WITH PYTHON SCRIPT 
  Serial.begin(9600);
  Serial.flush();
  Serial.println("<Arduino is ready>");
}

void loop() {
    radio.startListening();
    
    if( radio.available() ){                                             
      while ( radio.available() ) {                                   
        radio.read( &dataPack, sizeof(dataPack) );     
      }
      newData = true; 
    }

    if(newData == true){
      radio.stopListening();
      Serial.print(F("<Response: "));
      Serial.print(dataPack._value);
      Serial.println(F(">"));
      newData = false; 
    }

}

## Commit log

2020-06-06 Add ADCS component datasheets and schematics
2020-06-06 Remove old handdrawn controller schematic
2020-06-18 Close #5, sent a message between transceivers
    I used the code example from tutorial:
    https://howtomechatronics.com/tutorials/arduino/arduino-wireless-communication-nrf24l01-tutorial/
    I sent different texts to verify that the message
    was being sent correctly. If you are having trouble
    getting the tutorial to work, check the following:
    * The CE and CSN pin assignment is different in the
    tutorial than on the Amazon page. Make sure these
    pins are in the correct place.
    * Make sure that the baud rate of the serial monitor
    matches what is initialized in the code.
2020-06-19 Issue #9 - added STL files for single U frame as well as 3D printed gimbal prototype (using 608RS skateboard bearings)
    [Base Plate PC104.STL, Gimbal - inner_bearing_clip-1.STL, Gimbal - inner_ring-1.STL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]
2020-06-21 Python testing for basic motor and sensor - for use with single axis gimbal
2020-06-21 #10 Basic ADCS motor and pcb mount - next iteration needs battery and wiring plan
    [FIT0411_motor_frame.STL]
2020-06-25 Copy CMake config files from arduino-cmake repo
2020-06-25 Write basic test to print Hello World to serial
2020-06-25 Write doc for Arduino build system on Linux
2020-06-25 Write doc building Arduino code in WSLtty
2020-06-26 Move Arduino source files to a firmware directory
2020-06-26 Confirm Arduino will read and write from SD
2020-06-26 Test I2C connection between Arduinos
    I switched from using the Nano and Mega to using two Megas. The reason
    is that the Nano clone that shipped with the transceiver uses the old
    bootloader. I do not know how to select this bootloader using Arduino
    CMake.
    Also it is important to remember that the ports defined in
    'firmware/test/CMakeLists.txt' are specific to your computer and will
    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
2020-06-28 second iteration of gimbal assembly, utilizing self aligning bearings
    [GimbalMk2 - KFL08-1 608RS-1.STL, GimbalMk2 - connection-1.STL, GimbalMk2 - connection2-1.STL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]
2020-06-29 Build transceiver test with Arduino CMake
2020-07-10 added `MAX_TRQ.py` to test reaction wheel range of motion on testing bed and `P_TEST.py` to test proportional control
2020-07-10 control for testing with low friction string test bed
2020-07-10 Send char on serial to Arduino 1, I2C to Arduino 2
2020-07-11 Semi function control loop iteration, PWM control range of FIT0441 motor and accuracy of BNO055 on single axis need to be assessed - tested with string support
2020-07-14 Send image between devices using I2C
    To send image `./src/img/sent.jpg` between devices:
    1. Connect two Arduino Mega's to the host computer. Connect the two
    Arduinos together using an I2C connection i.e. connect 20 and 21 to
    each other, and connect the grounds of the two Arduinos.
    2. Load `server` executable on one, and `client` on the other. Right
    now the ports `/dev/ttyS8` and `/dev/ttyS9` are hardcoded into
    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
2020-07-14 Partially send image between Arduinos
    This code sends an image between the two Arduinos but currently it is
    corrupted. The beginning of the message header is never sent correctly.
    To inspect yourself:
    flash one Arduino with the `server.cpp` and the other with `client.cpp`.
    run `recieve.py` and then `send.py`
    inspect resulting `received.jpg` in hex editor to see the differences
2020-07-15 Add README for firmware directory
    Gives build instructions as well as how to add Arduino libraries to
    local system so that Arduino CMake can find them.
2020-07-15 Build and run RadioHead example
    Adds the source code and build instructions for the RadioHead nrf24
    client (https://www.airspayce.com/mikem/arduino/RadioHead/nrf24_client_8pde-example.html)
    and server (https://www.airspayce.com/mikem/arduino/RadioHead/nrf24_server_8pde-example.html)
    examples. The example doesn't work and fails with:
    No reply, is nrf24_server_running
    Even though server does seem to be running. I will check for errors
    after lunch.
2020-07-15 Rename existing files to adhere to Google styleguide
    [GimbalMk2 - KFL08-1 608RS-1.STL, GimbalMk2 - connection-1.STL, GimbalMk2 - connection2-1.STL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]
2020-07-15 Get example from RadioHead working on Mega's
    The problem was that the hardware connections to initialize RadioHead between
    the nRF24L01 and the Mega's was different than the previous library. The
    documentation is here (http://www.airspayce.com/mikem/arduino/RadioHead/classRH__NRF24.html#abe13cbb557450abdd90ee12256deeb6e).
    You can find the Mega entry by Ctrl-F. For different hardware the
    initialization of the RH_NRF24 class will have to be different.
2020-07-15 Change comms firmware for Arduinos to be the same
    Before there was a transmitter.cpp/receiver.cpp or client.cpp/server.cpp
    for the Arduinos. I think the two Arduino's can actually run the same
    code and the Python scripts dictate the server/client. I am now going to
    try and implement the KISS protocol in a python script.
2020-07-27 Add pi-arduino testing files
2020-07-31 Add comments to transceiever Arduino code
2020-08-08 Basic arduino program using RTOS.
2020-09-18 added debug statements, changed main()
    [gimbal-assembled.stl, sat-frame-oneu.stl]
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2020-11-01 updated message display for gui
    [gimbal-assembled.stl, sat-frame-oneu.stl]
2020-11-01 work_with_sat renamed, added rx and tx role switch
2020-11-26 included test file gs.py
    [gimbal-assembled.stl, sat-frame-oneu.stl]
2020-11-26 update ground_station w/w gs.py + satellite.ino
2022-06-02 hardware: change dir name from stl-files to hardware
    [GimbalMk2 - KFL08-1 608RS-1.STL, GimbalMk2 - connection-1.STL, GimbalMk2 - connection2-1.STL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]
2022-06-02 stl-files: rename dir from stl-files to hardware
    [GimbalMk2 - KFL08-1 608RS-1.STL, GimbalMk2 - connection-1.STL, GimbalMk2 - connection2-1.STL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]
2022-06-04 radio: inherent base Arduino class
2022-06-05 common: arduino: support serial communication
2022-06-05 common: arduino: support generic i2c communication
2022-06-05 requirements: include smbus for I2C communication
2022-06-12 main: clean up print messages
2022-07-07 src: common: arduino: make serial commands more robust
2022-07-07 src: comms: radio: use arduino to transmit and receive
2022-07-13 common: include Arduino parent class information
2022-07-13 src: common: readme: include Arduino connections
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2022-07-24 src: comms: radio: import rather than inherient Arduino class
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2022-09-29 hardware: stl: prepare stl files for 3D printing
    [bracket-rpi4.stl, rack.stl, rail.stl]
2022-09-30 hardware: add jerome's mock-sat chassis
    [Siderib-U.SLDPRT, Siderib-U.STL, baseplate 2.SLDPRT]
2022-10-08 hardware: mock-sat-1u: stack with rails instead of rack
2022-10-08 hardware: stl: create stl files of new rail and rack
    [rack.stl, rail.stl]
2022-11-01 hardware: 1U: new bracket for rpi
    [shelf-rpi.stl]
2022-11-05 hardware: stl: create shelfs for standardly used components
    [bracket-rpi4.stl, shelf-blank.stl, shelf-nucleo.stl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]
2023-03-16 groundstation: gui: make a simple tkinter gui builder
